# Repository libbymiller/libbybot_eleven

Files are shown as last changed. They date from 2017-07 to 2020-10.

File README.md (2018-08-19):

# libbybot_eleven

Eleventh incarnation of 
[libbybot](https://planb.nicecupoftea.org/2017/03/03/libbybot-presence-with-chromium-51-raspberry-pi-and-rtcmulticonnection-for-webrtc/), a cheapo, remotely-posable presence robot using [webRTC](https://en.wikipedia.org/wiki/WebRTC) and a Raspberry Pi, currently living in an IKEA lamp

Contains full instructions and code. 

Libbybot 8

The idea is that you run a headless browser on a Raspberry Pi in the lamp, and connect to it remotely via a laptop or phone using a browser (Chrome or Firefox).

You need to do the [server](/server) part of this first, then set up the [arduino](/arduino) and [pi](/pi). Construction instructions are in [doc](doc/)

## What you'll need:

 * Time: this takes a few hours at least even if you know what you are doing. It's not a quick project.
 * Raspberry Pi 3 (other versions don't have the oomph to run chromium and do video, though they can do audio, if you don't want to "see").
 * an official [Raspberry pi power cable](https://shop.pimoroni.com/products/raspberry-pi-universal-power-supply) - we're using a lot of amps! else you may get strange outages.
 * IKEA EXPRESSIVO lamp (discontinued, but most people have one at home, ask around). Or [this (thanks Barnoid!)](http://cpc.farnell.com/lloytron/l1101bk/lamp-desk/dp/LA04023) looks very similar.
 * [long (45cm) Raspberry Pi camera cable](https://shop.pimoroni.com/products/raspberry-pi-camera-cable)
 * [Raspberry Pi camera](https://shop.pimoroni.com/products/raspberry-pi-camera-module-v2-1-with-mount)
 * a [Sennheiser USB speaker / mic](http://www.exteradirect.co.uk/product/sennheiser/sp20-portable-speakerphone-usb-&-3.5mm/3258/)
 * 2 x 9g servos, small as you can get them ([e.g.](http://www.ebay.co.uk/itm/Mini-SG90-SG-90-Gear-9g-Micro-Servo-For-RC-Airplane-Helicopter-Car-Boat-Arduino/252297215595)). The blue type are the ones you need - the black ones are fractionally too long.
 * a [tiny breadboard](https://shop.pimoroni.com/products/colourful-mini-breadboard)
 * 6 x MM jumper cables 
 * 3 x MF jumper cables 
 * Arduino nano (e.g. a [clone](http://www.ebay.co.uk/itm/Mini-USB-Nano-V3-0-ATmega328P-CH340-5V-16MHz-SOLDERED-HEADS-Arduino-UK-/262738901345))
 * an old CD or a [custom laser cut shape](doc/laser_cut_base) - and 6 x 3mm diameter ball barings
 * little rubber feet ([e.g.](https://www.amazon.co.uk/Domed-Rubber-Buffers-Kitchen-Doors/dp/6040143746/ref=sr_1_1))
 * 1 thin small cable tie
 * two pieces of 2cm x 1cm x 3mm (or 1 x 5-6mm) plastic or something equally tough
 * two M2 plastic bolts

and

 * Something to cut holes in the lamp's plastic like a dremel (you can just about manage with a hacksaw and drill, but it's messy) plus suitable eye protection
 * a hacksaw
 * a phillip's head screwdriver
 * a gluegun
 * a vice
 * a pen
 * a tape measure

and, once you're up and running

 * a friendly helper in the remote place where you want to be, to plug the lamp in

The only really expensive thing is the speaker / mic. If you're going to use it seriously, this is the most important bit. I've tried a Jabra for this purpose but they are unreliable, I'm guessing they have heavier power 
requirements than the Sennheiser. The Sennheiser works really well - the best I've come across for this sort of thing.

Of course you don't have to use an IKEA ESPRESSIVO lamp. This project originally started off much more like a picture frame - you can see the pictures [here](https://planb.nicecupoftea.org/2017/03/03/libbybot-presence-with-chromium-51-raspberry-pi-and-rtcmulticonnection-for-webrtc/) - but it's hard to fit the speaker into some sort of sensible shape. My robot research has shown that showing my face to the participants of a teleconference is not necessary as long as I can hear, speak, see and move  a little (in that order).

More on how to actually fit it into the lamp is in [doc](doc/).

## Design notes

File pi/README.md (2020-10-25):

# Introduction

The idea is that you run a headless browser on the pi, and connect to it 
via a laptop or phone using a browser. 

You'll need a [server](/server) to connect to first.

More on how to actually fit it into the lamp, including assembling everything, is in 
[doc](doc/).

# Installation

This is mostly a matter of making sure the audio and video drivers are 
in place, and then running chromium on boot, together with a simple 
python server for controlling the servos.

## Set up the Pi with Buster (not Buster-lite)

[Here are full instructions for burning an SD card](https://www.raspberrypi.org/documentation/installation/installing-images/) or use [Etcher](https://etcher.io).

When it's done, still with the SD card in the card reader (you may have to unplug the reader / plug it in again), do

    touch /Volumes/boot/ssh 

(This is on a Mac; other OS you need to figure out where `boot` is mounted and create an empty file)

[Add in your wifi network creds](https://www.raspberrypi.org/blog/page/2/?fish#another-update-raspbian) to /Volumes/boot/wpa_supplicant.conf:

    nano /Volumes/boot/wpa_supplicant.conf

contents (the country first line is important, though it doesn't have to be GB, obviously):

    country=GB
    ctrl_interface=DIR=/var/run/wpa_supplicant GROUP=netdev
    update_config=1

    network={
       ssid="foo"
       psk="bar"
    }

or if you're going to move it around, you could [try this](https://planb.nicecupoftea.org/2015/12/04/raspberry-pi-create-an-access-point-for-easily-getting-limited-input-devices-on-wifi-chromecast-style/).

Eject the SD card and put it in a Pi3.

Log in, e.g. by using a screen and keyboard and mouse or by sharing your 
network over ethernet and sshing in, or sshing in over your network if 
you added the `wpa_supplicant.conf` credentials as above.

## Add audio and video drivers

    sudo nano /etc/modules

contents:

    i2c-dev
    snd-bcm2835
    bcm2835-v4l2

(bcm2835-v4l2 is the V4l2 video drivers for Chromium to pick up the camera; there used to be a [bug](https://stackoverflow.com/questions/25941171/how-to-get-gstreamer1-0-working-with-v4l2-raspicam-driver) but not any more)

## Enable USB audio

    sudo nano /boot/config.txt 

in contents

    #dtparam=audio=on ## comment this out

then

    sudo nano /lib/modprobe.d/aliases.conf

in contents

    #options snd-usb-audio index=-2 # comment this out

(I find USB audio on the linux / Pi very tricky and I'm not the only one. However, in 
recent Raspian versions USB audio seems to Just Work. The above is belt and braces. 
[More on linux 
audio](http://raspberrypi.stackexchange.com/questions/39928/unable-to-set-default-input-and-output-audio-device-on-raspberry-jessie).)

## Give the GPU more oomph

This is optional, but you'll get smoother video performance at the cost of the chip getting hotter...! ([more info](https://raspberrypi.stackexchange.com/a/1885)).

Edit config.txt

    sudo nano /boot/config.txt  

contents - add or edit:

    gpu_mem=192 

## Add autostart

    sudo nano /etc/xdg/lxsession/LXDE-pi/autostart

contents:

    @lxpanel --profile LXDE-pi
    @pcmanfm --desktop --profile LXDE-pi
    @xscreensaver -no-splash
    @xset s off
    @xset -dpms
    @xset s noblank
    #@v4l2-ctl --set-ctrl=rotate=270 # if you need to rotate the camera picture
    @/bin/bash /home/pi/start_chromium.sh

Add the files start_chromium and server.py from this directory into the pi 
homedirectory. Edit ```start_chromium.sh``` to refer to your server.

Make them executable:

    chmod a+x start_chromium.sh server.py

install the python server

    sudo pip install bottle

enable the camera and serial in ```interfacing options``` using

    sudo raspi-config

for serial, select 'no' for 'would you like a login shell to be accessible over 
serial?' and 'yes' to 'Would you like the serial port hardware to be enabled?'

Change the pi name and password

    sudo nano /etc/hostname
    sudo nano /etc/hosts
    passwd

## Assemble everything and test

Shutdown and unplug the pi, then - 

 * [connect the camera to the pi](https://www.raspberrypi.org/documentation/usage/camera/README.md)
 * connect the sennheiser to the pi
 * plug in the pi's power again

On your-server, check the logs of `server.js` and you'll see the number of the room 
it's connected to.

Connect to https://your-server:8443/remote.html#roomnumber on a laptop, 
in Chrome or Firefox. You should see whatever the Pi's camera is pointing at, 
and be able to hear too, and speak. 

Longer term, you need to figure out how to do notifications. There's a place in 
[server.js](/../server/server.js) where you can send a dm tweet or a slack notification 
for example.

More on how to actually fit it into the lamp, including adding the Arduino, is in 
[doc](doc/).

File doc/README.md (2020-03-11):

# Introduction

Allow a few hours for this.

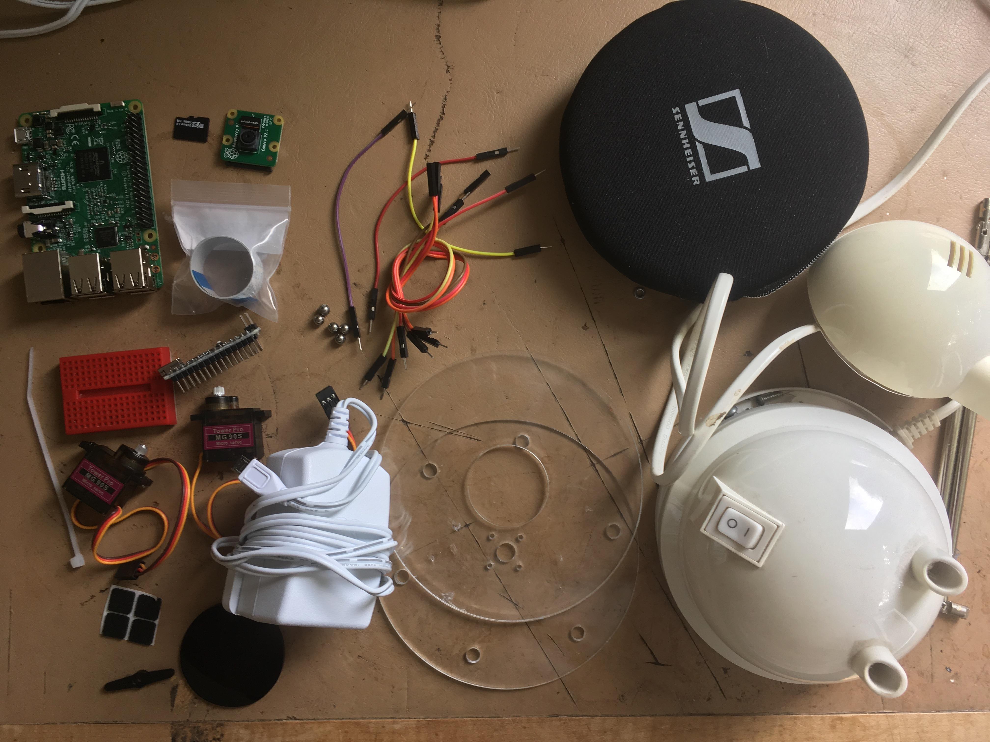
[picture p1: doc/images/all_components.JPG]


The idea is to hollow out the base to fit a Pi and and Arduino in it, and fit tiny servos to the top part (the 'head') and the base.

## Modify the case

Take your EXPRESSIVIO lamp, making sure it is unplugged from the mains, obviously, unscrew the base and remove and discard the transformer and related pieces, together with the power cable.

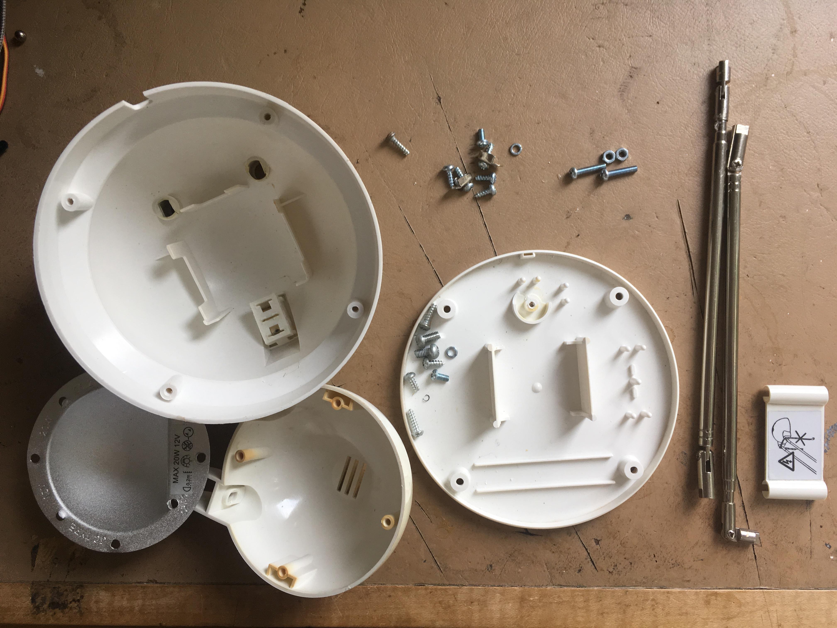
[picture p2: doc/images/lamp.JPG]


Remove the glass plate from the top, and the bulb and any bits of wires connected to it.

With pliers, snap off the inside segments of both parts of the base to make as much room as you can. 

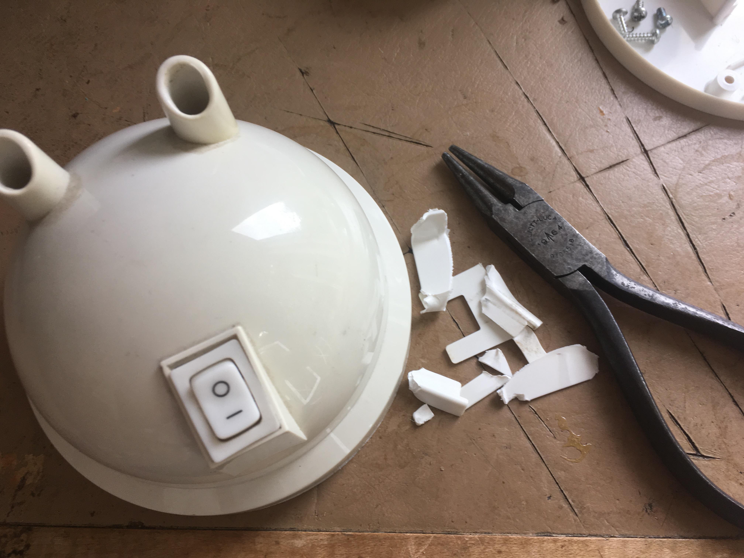
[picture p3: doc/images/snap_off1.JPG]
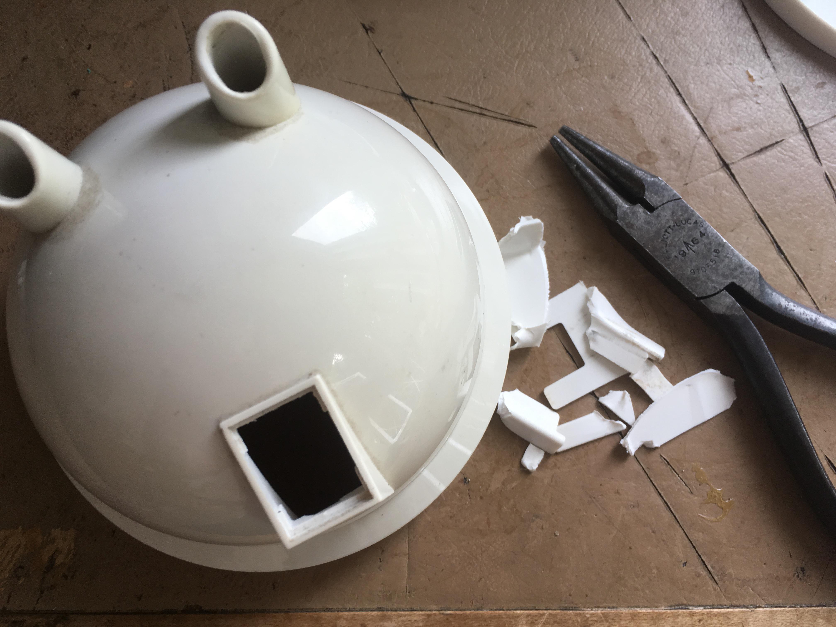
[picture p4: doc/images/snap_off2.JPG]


Carefully saw the backs off the top ariel covers. Don't saw off too much - just up to the curved point to make a straight line, and then saw the corner off the inside of each one.

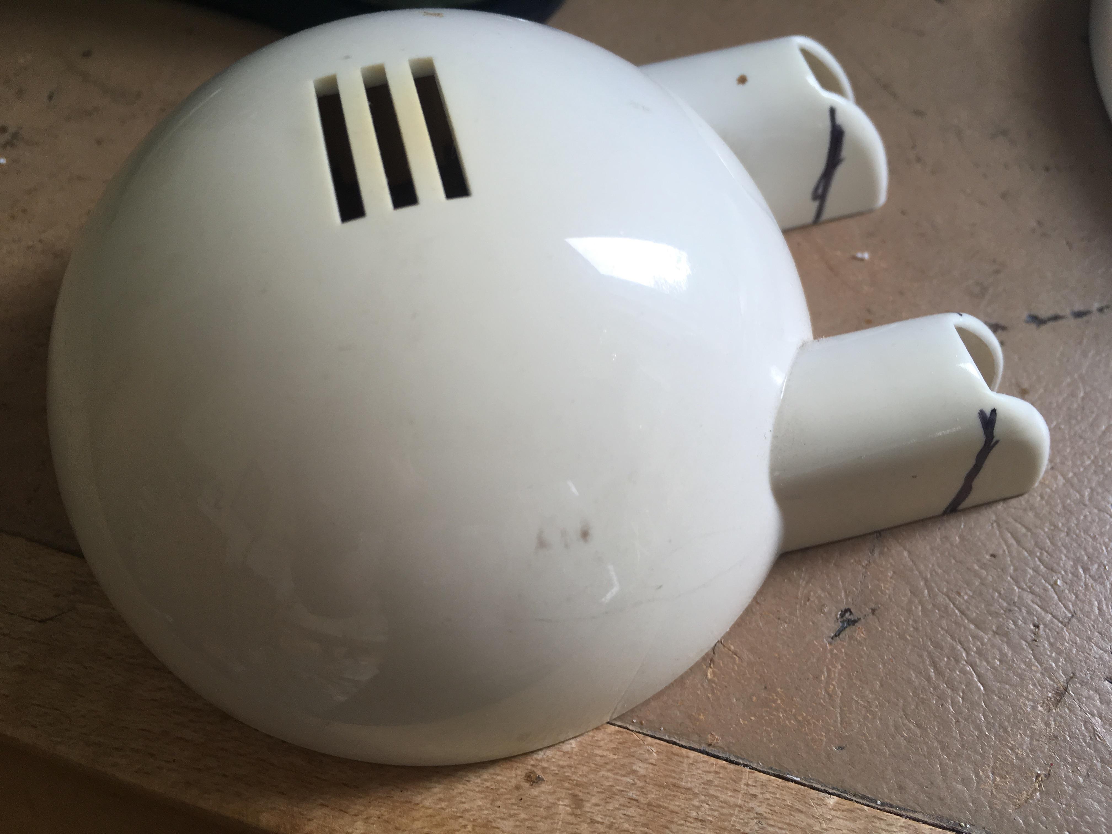
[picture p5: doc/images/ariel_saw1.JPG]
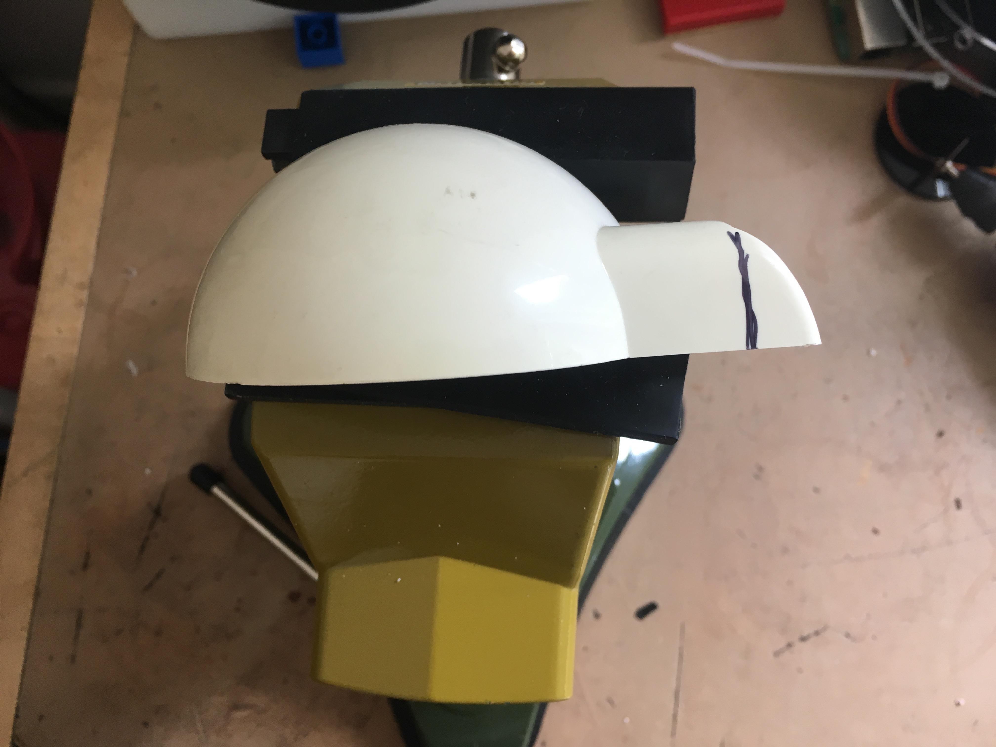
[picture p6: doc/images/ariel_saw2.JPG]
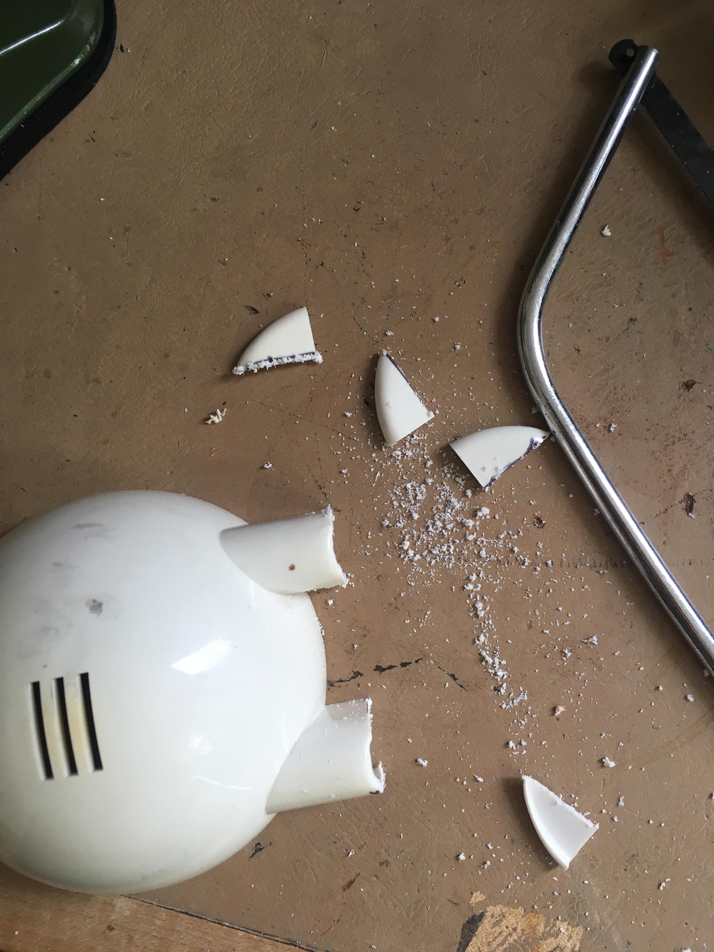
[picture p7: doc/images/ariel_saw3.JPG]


Saw or dremel a hole in the back of the base. This needs to be wide and deep enough to get a USB cable and a wifi camera cable into (it's also sometimes useful to be able to get the Ethernet cable in too if possible). About 1cm x 4cm half way between the bottoms of the ariels and the rim of the base will do the job. Tidy it up with sandpaper.

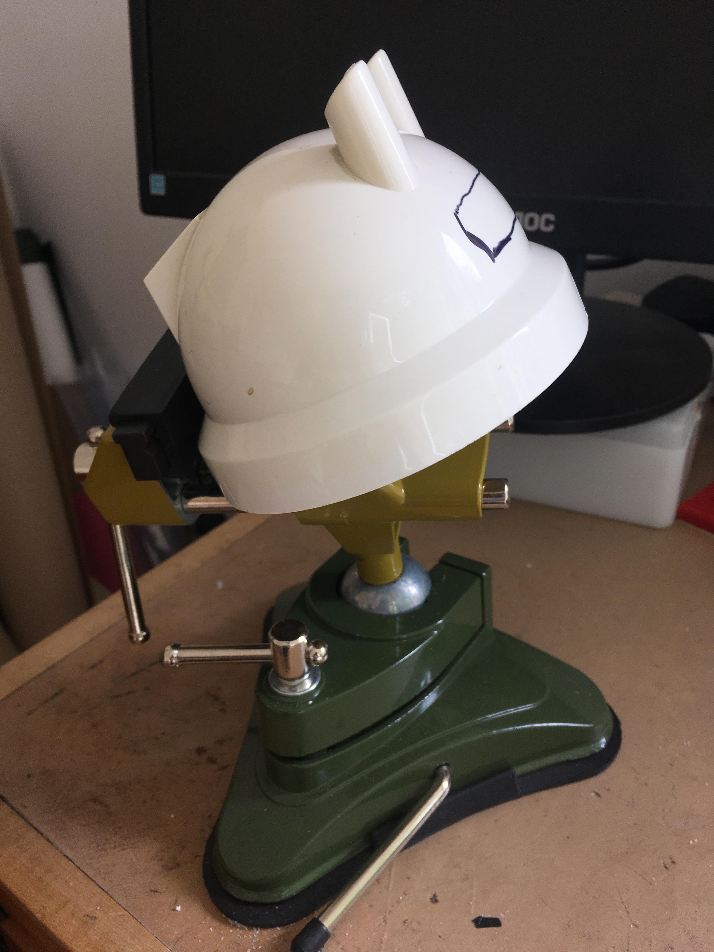
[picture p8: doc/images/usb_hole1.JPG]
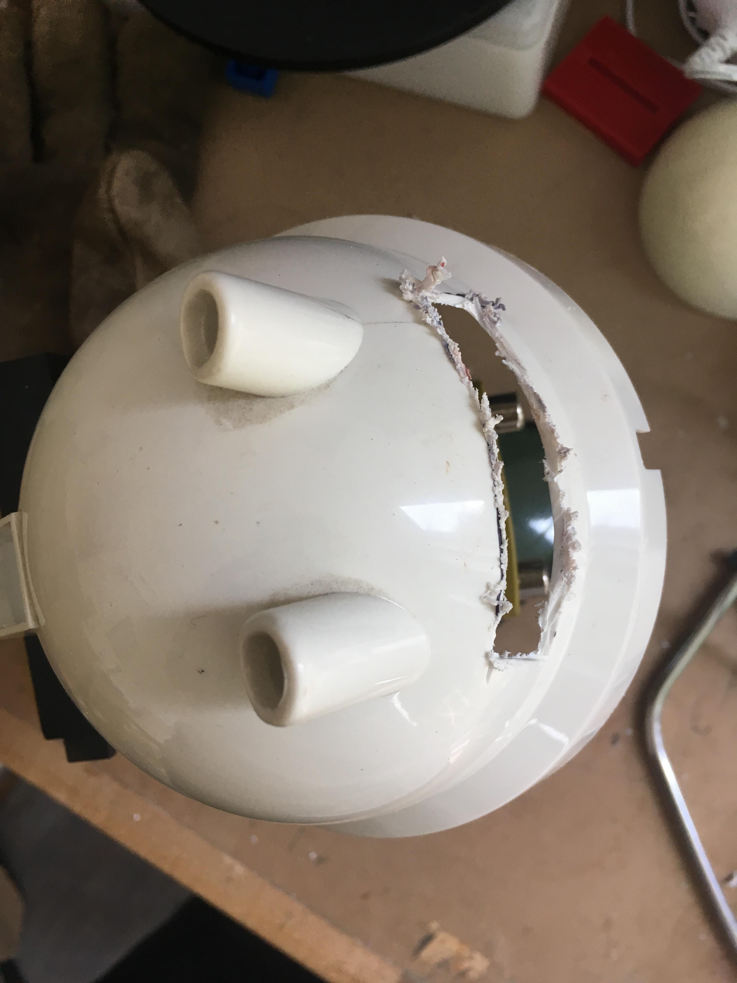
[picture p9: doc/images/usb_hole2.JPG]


Dremel or drill two holes in the centre of the flat base panel such that the servo exactly fits. 

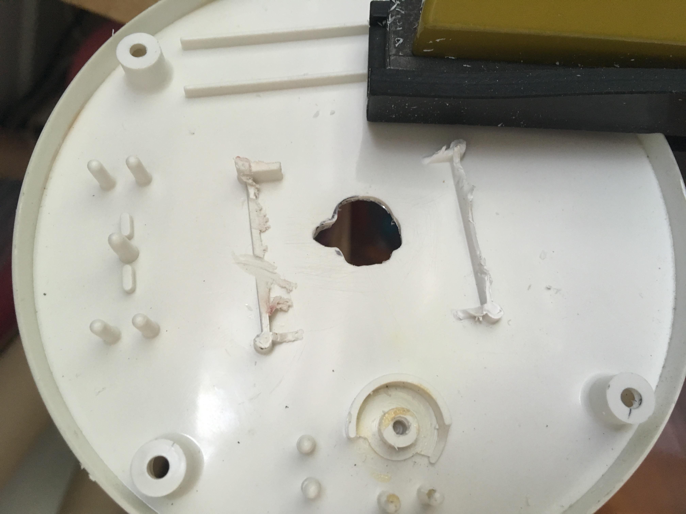
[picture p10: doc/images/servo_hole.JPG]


You'll also need to saw a small wedge out of the base to fit the power supply cable in. It's easier to do this at the end - see below.

## Connect the top servo

 * flash the arduino with the code in [arduino](/arduino)
 * push on the servo's one-sided horn (the plastic bit that you attach to the motor itself) - but don't screw it on yet
 * connect the servo to 5V (red), GND (brown or black) and D4 (orange)

Hold the servo with the horn facing you.

In the serial part of the arduino IDE, type "2 10". This is the lowest point for the 'head'. Re-position the horn if need be so it's parallel to the body of the servo.
 
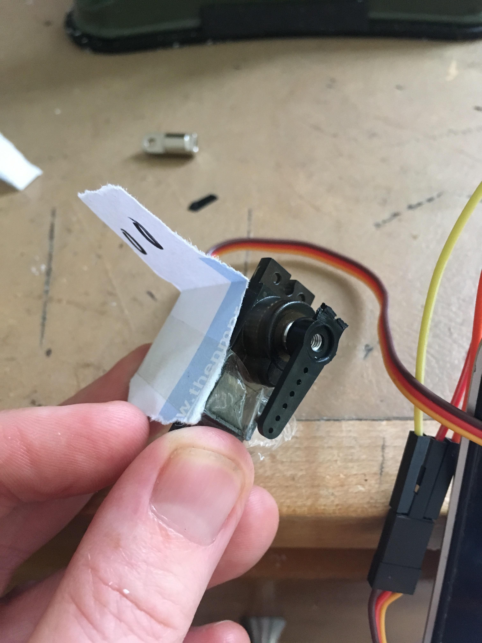
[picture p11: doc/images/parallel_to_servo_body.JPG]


Now type "2 60" in the Arduino IDE. This is the highest point of the head. Holding the horn with it facing you, the body of the servo should turn clockwise by 50 degrees. Type "2 10" again to get it back to its starting position. 

Now reassemble and position the lamp:
 * tighten the ariel's bottom screws as tight as they go
 * move the lamp so its head is as far bowed as it will go.

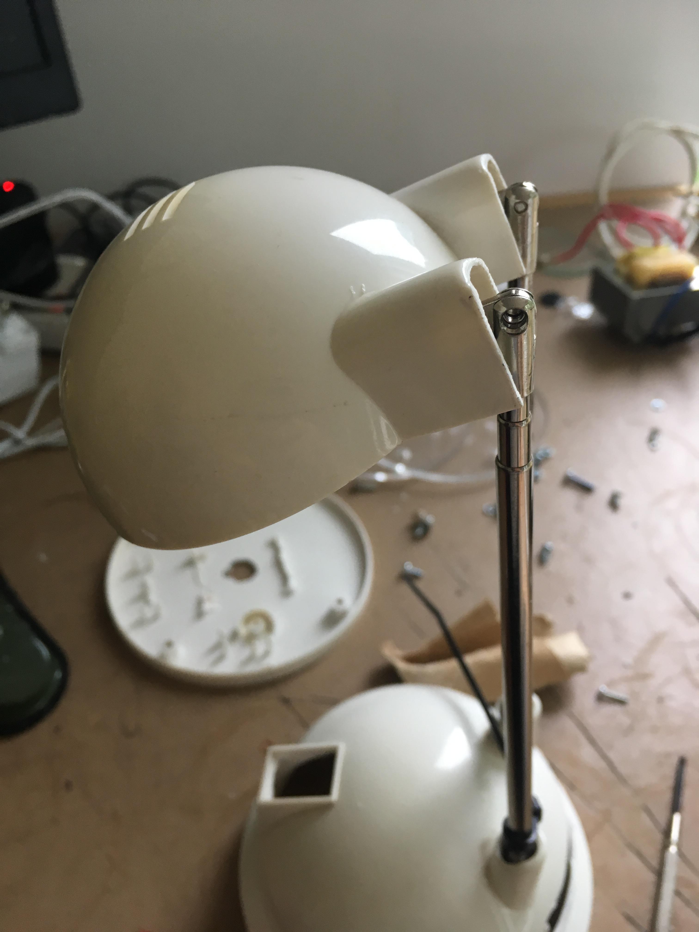
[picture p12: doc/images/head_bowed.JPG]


Replace the right hand screw at the top of the lamp with a servo and a screw through its spindle (you'll need to find a screw that's a bit longer than the usual one). Cable-tie the servo's horn to the downward ariel. Loosen the other screw so it is mobile.

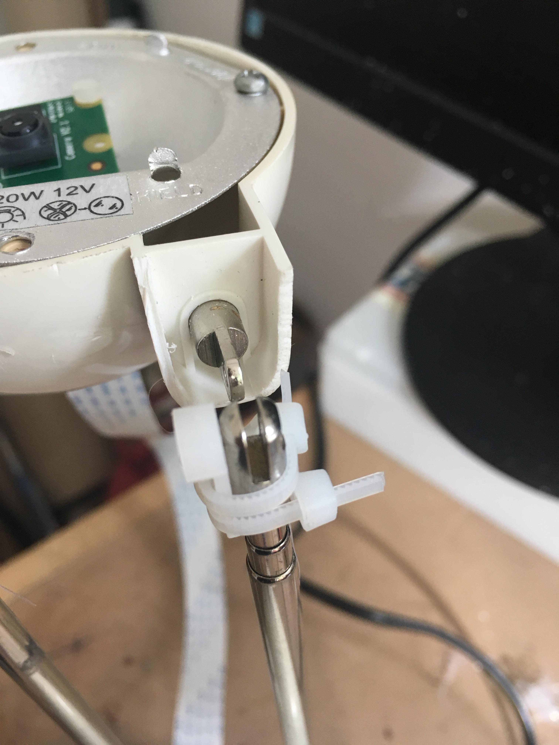
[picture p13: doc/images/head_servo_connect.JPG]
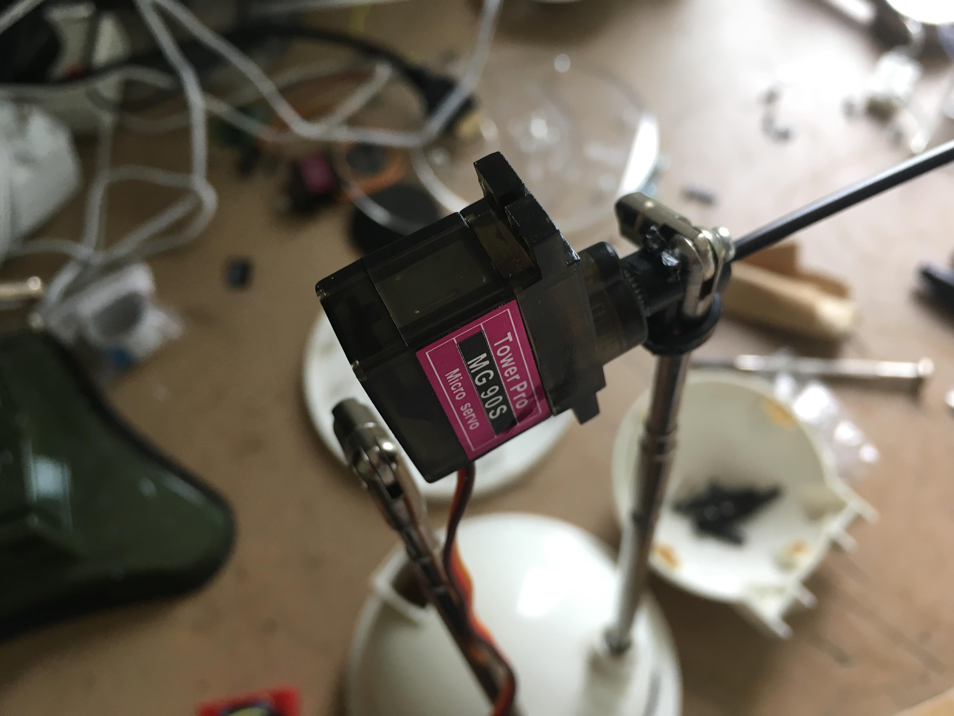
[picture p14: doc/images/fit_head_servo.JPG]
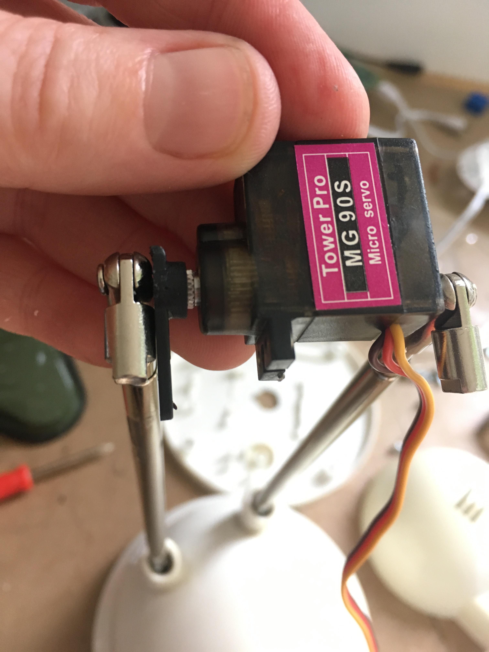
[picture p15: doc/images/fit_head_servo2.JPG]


Glue-gun one or two of the flat plastic pieces between the servo and the bottom of the lamp top (how many you need depends a bit on your servo's size and how much plastic you took off the lamp).

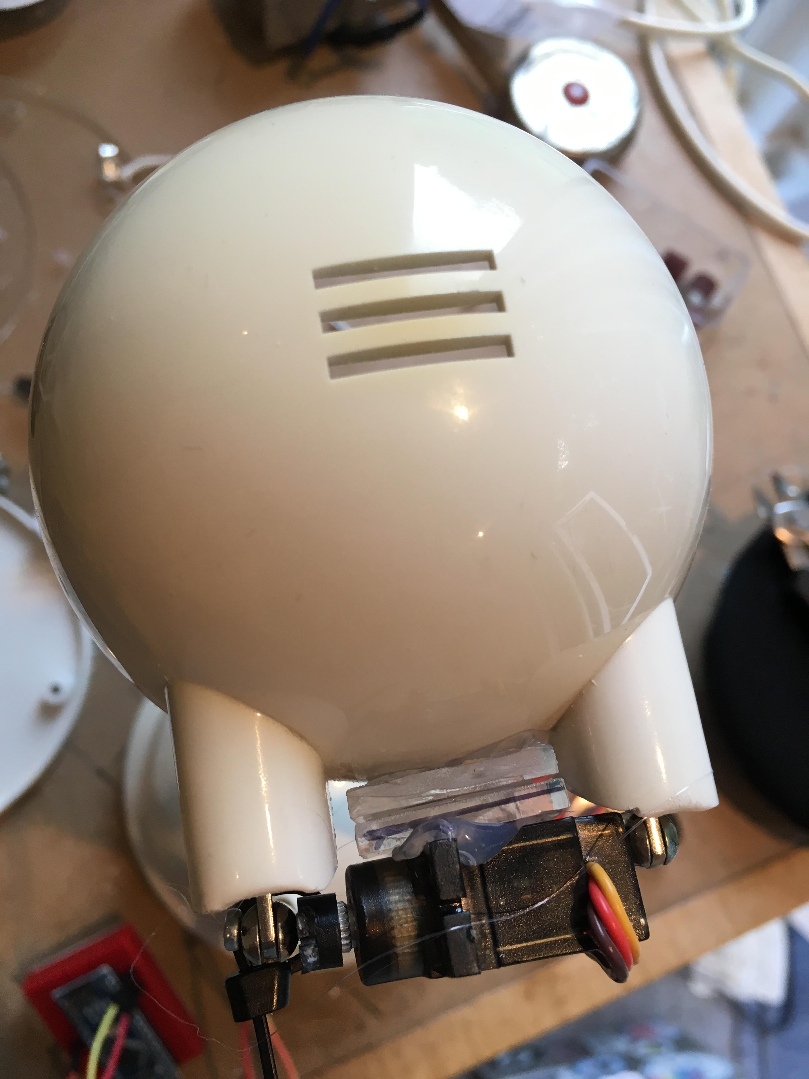
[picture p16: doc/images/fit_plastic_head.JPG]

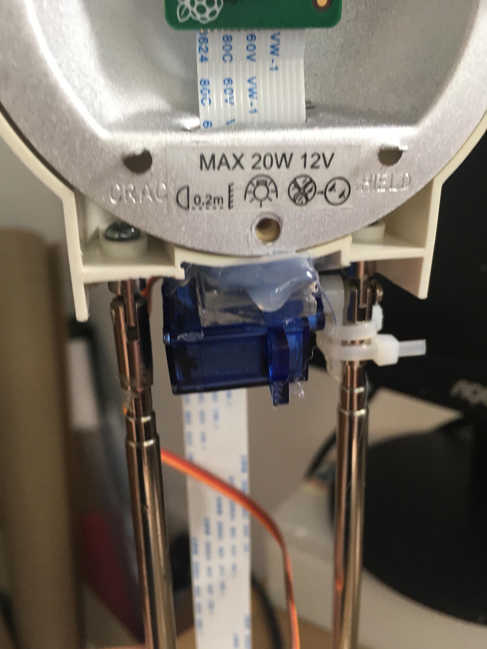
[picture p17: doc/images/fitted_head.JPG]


Test the servo again.

## Connect the bottom servo

 * connect the servo to 5V, GND and D3 (orange)
 * Figure out where 90 degrees is (using ("1 90") in serial)

Place that point at the front of the lamp.

Wedge the servo into the holes you made, glue-gunning it in as well.

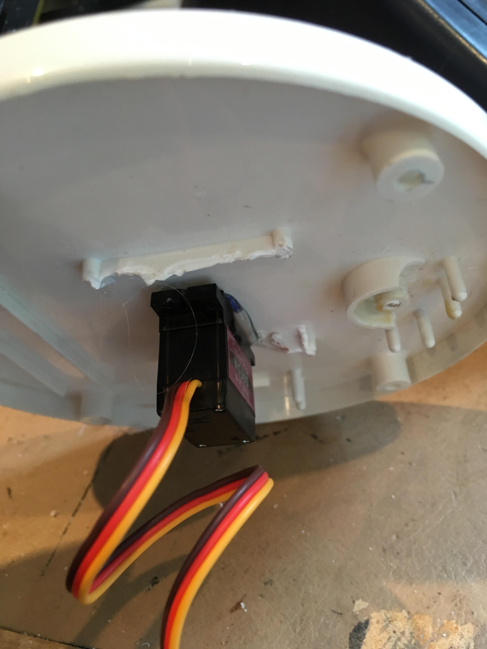
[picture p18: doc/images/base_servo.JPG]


When the glue has dried, test the servo again (e.g '1 10' '1 90' '1 170').

## Connect the arduino and the Pi

We're using a serial connection to save space.

On the Arduino you should have the top servo connected to pin D4 and the other to pin D3.

Connect:
 * 5v on Pi to 5v on the arduino (e.g. [GPIO physical numbering](https://www.raspberrypi.org/documentation/usage/gpio/) 2 or 4)
 * ground on the Pi to ground on the Arduino (e.g. GPIO physical numbering 6, 9 etc)
 * Pi's TDX (GPIO physical numbering pin 8) to Arduino's RX

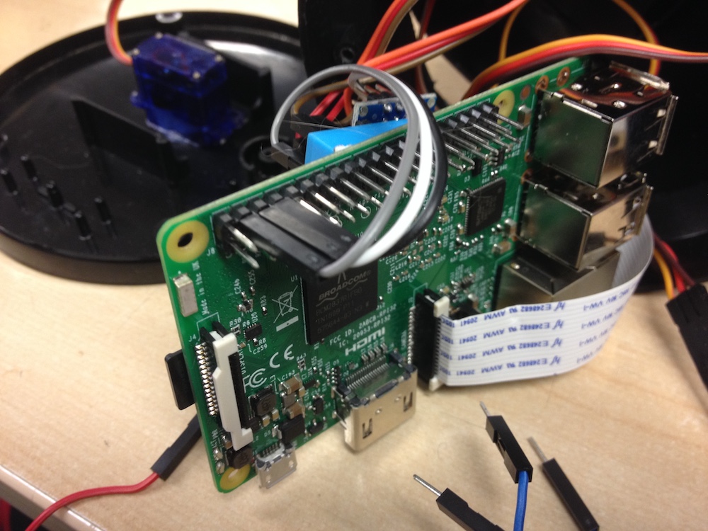
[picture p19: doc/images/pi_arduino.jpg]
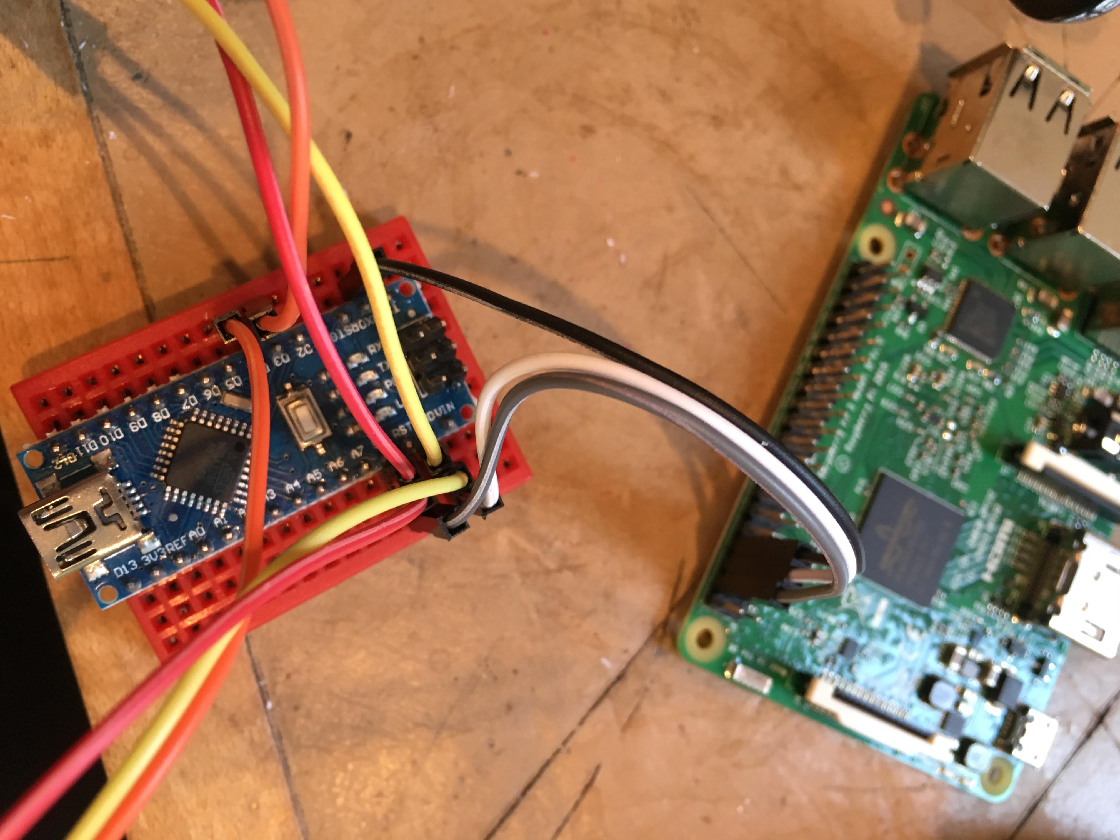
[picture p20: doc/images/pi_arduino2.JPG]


Normally you'd [need a voltage divider](https://oscarliang.com/raspberry-pi-and-arduino-connected-serial-gpio/) 
to do this serial communication, but because we're only going one way - from the 
Pi to the Arduino - we get away with it.

Stick or rest the breadboard to the back of the Pi.

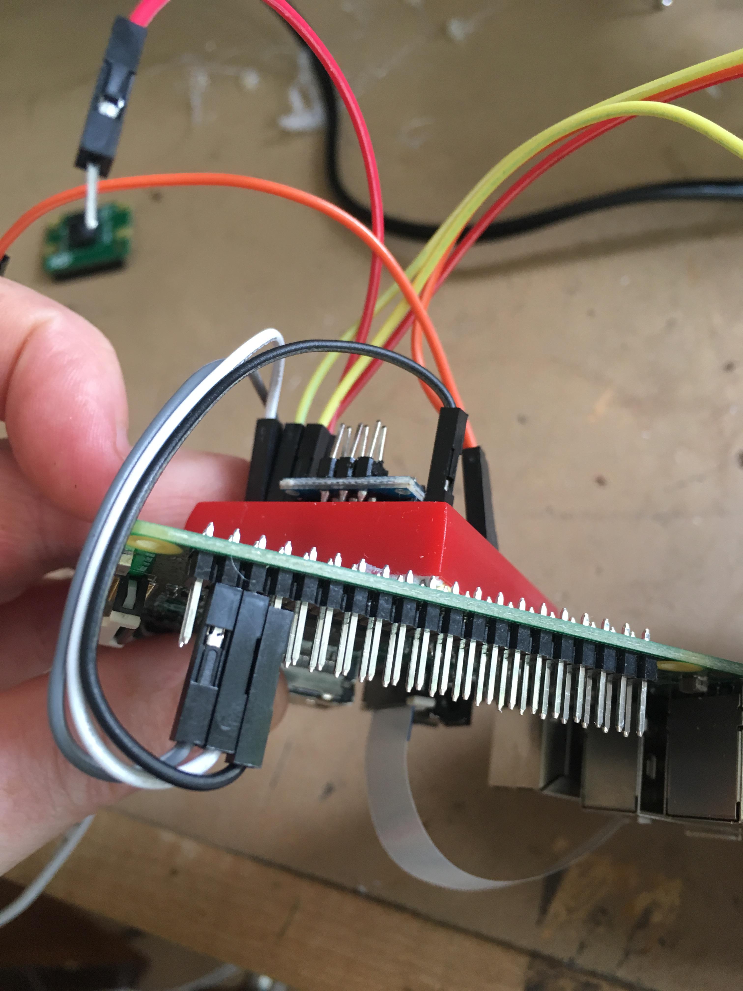
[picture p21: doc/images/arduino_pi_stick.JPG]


## Add the camera

Carefully widen the slit in the aluminum case at the bottom and thread the extra long camera cable through it. Connect and position the camera, screwing it (using plastic screws if you do) or glueing it into place.

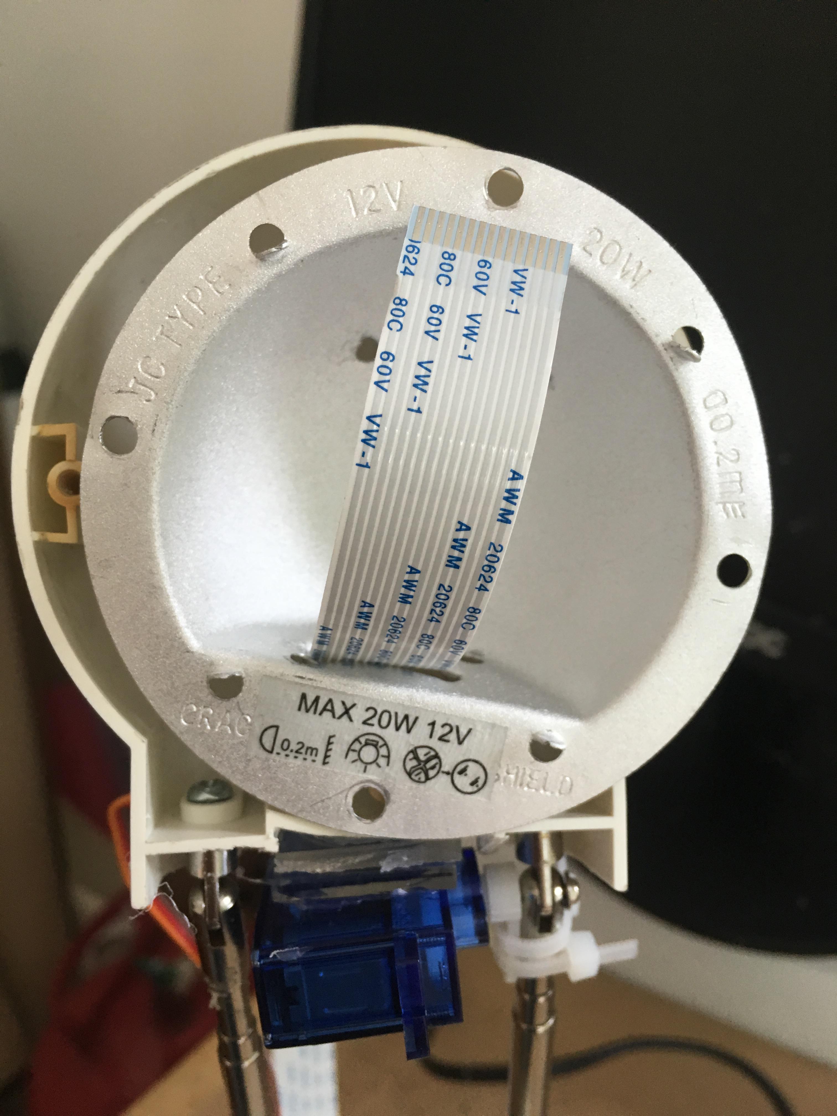
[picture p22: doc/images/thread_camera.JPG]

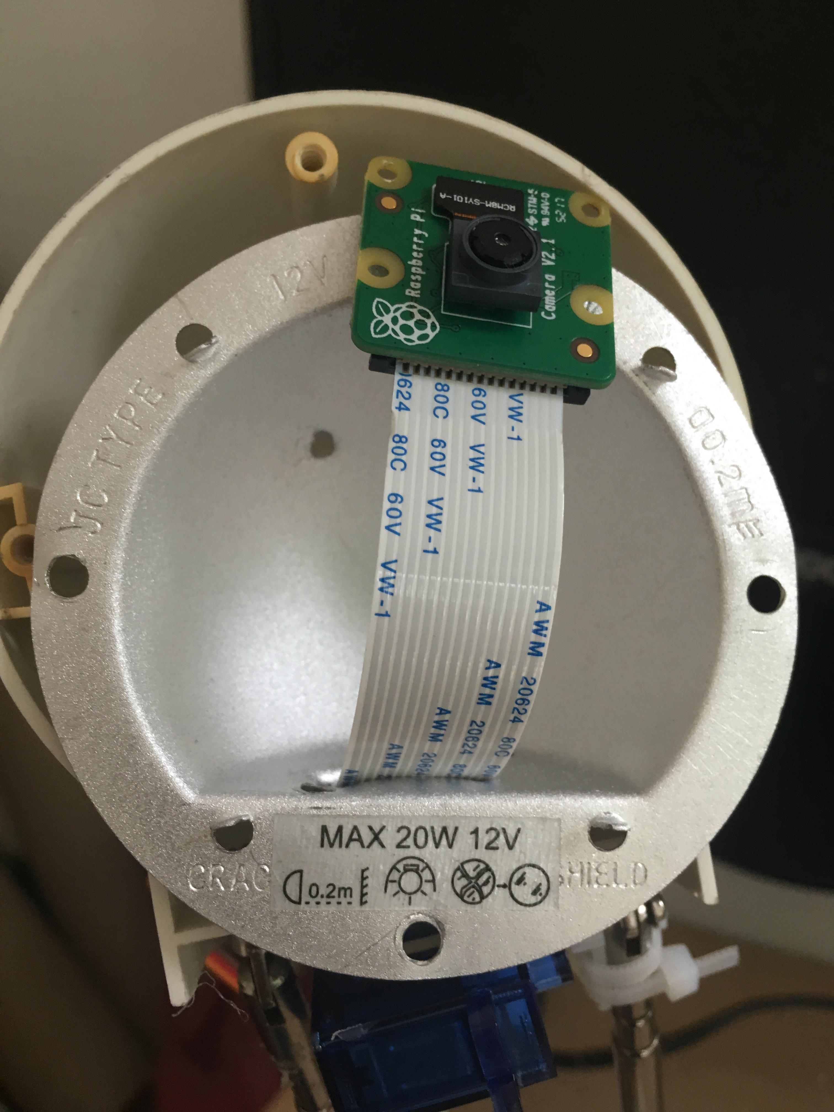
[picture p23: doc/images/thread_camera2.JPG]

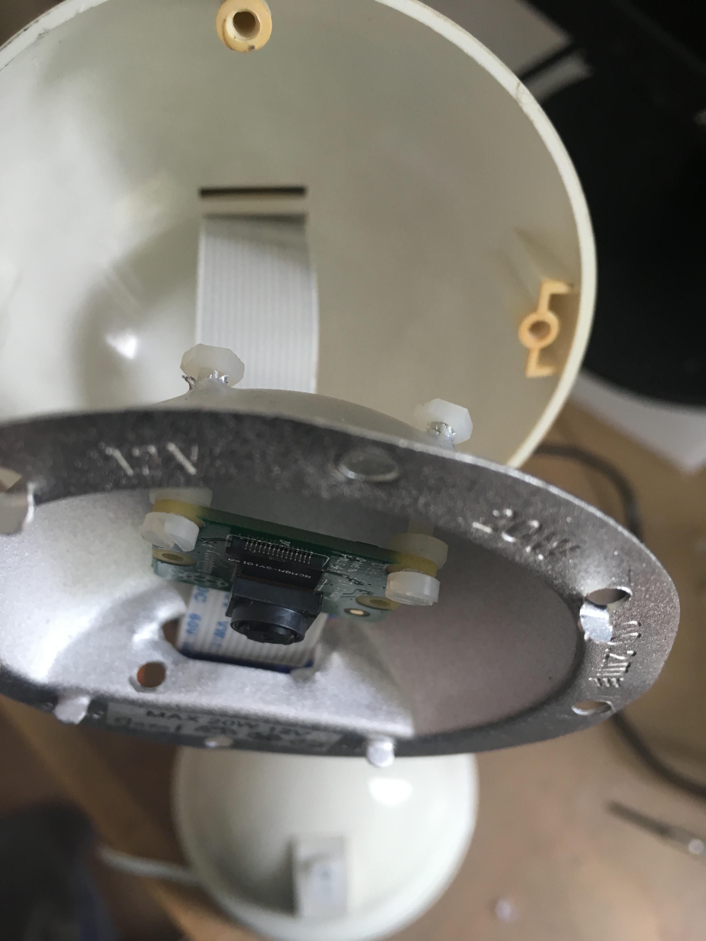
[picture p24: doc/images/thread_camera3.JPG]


Feed the other end into the slot you made in the base and attach it to the Pi (making sure the Pi is unplugged and that you're connecting it the [right way round](https://thepihut.com/blogs/raspberry-pi-tutorials/16021420-how-to-install-use-the-raspberry-pi-camera).) 

<a href="images/camera_base.JPG">

## Connect everything together

This is quite a wedge and it's why you need the smallest 9g servo you can find.

Basically the Pi goes in the bottom at an angle with the breadboard underneath the Pi. It needs to be placed at a downward angle so that the USB port is accessble through the slot, and so that there's room for the servo and the servo isn't squishing the camera cable.



First, make sure you've programmed the Arduino and got the Pi on the network you want to use it on, and that you've connected the Arduino via serial to the Pi (see above). You can't reprogramme the Arduino once it's in because it can't be programmed with the serial attached.

Connect the power cable to the Pi, and, making sure you have the lamp base the right way round (there's a notch at the back) carefully mark and saw a wedge out of the base for it to fit. It must not be forced or bend! You may also need to saw off the top of one of the base plate's screw casings (make sure you get the right one).

<a href="images/power_hole2.JPG">

Connect the Sennheiser through the slot to the USB port.

This is a good time to test everything works - plug it in and check the server for messages about the url to use and load the url in Chrome. 

If all is well, replace the bottom plate - you may need to twist it slightly to get it on its rails. Screw it on, omitting the screw near where you cut the notch. 

If you have laser-cut the base components in the [laser_cut_base](laser_cut_base/) directory, glue the servo horn to base 1 with the notch facing through the hole, glue base 2 to base 1, put the ball bearings in the holes and attach the 
two parts of the servo together, screwing them in. Otherwise, glue the servo horn part to the CD base and add rubber feet.



If all is well, you're ready to go. Plug it in!

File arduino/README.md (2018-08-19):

# Introduction

This is a very simple piece of code that expects commands over serial of the form:

    number degrees [p|n]

e.g. 

```1 90``` means turn servo 1 to absolute position of 90 degrees.

```1 10 p``` means turn servo 1 10 degrees in a positive direction.

```2 10 n``` means turn servo 2 10 degrees in a negative direction.

Servo 1 is the base (rotating) and goes in arduino pin 3. Servo 2 is the "head" of the lamp (nodding, etc) and goes in arduino pin 4. Servos 3 and 4 are not used (I'm using them in later versions to give the shoulders more sass).

[server.py](../pi/server.py) uses groups of these commands passed through from the web browser via webRTC sockets and passes them via serial to the arduino.

# Installation

If you are using a Nano clone, you'll need 
[drivers](https://kig.re/2014/12/31/how-to-use-arduino-nano-mini-pro-with-CH340G-on-mac-osx-yosemite.html).

Note that you'll need to disconnect the serial connection from the Raspberry pi to flash the arduino (this catches me out every time). And then plug it back in again (this also catches me out every time).

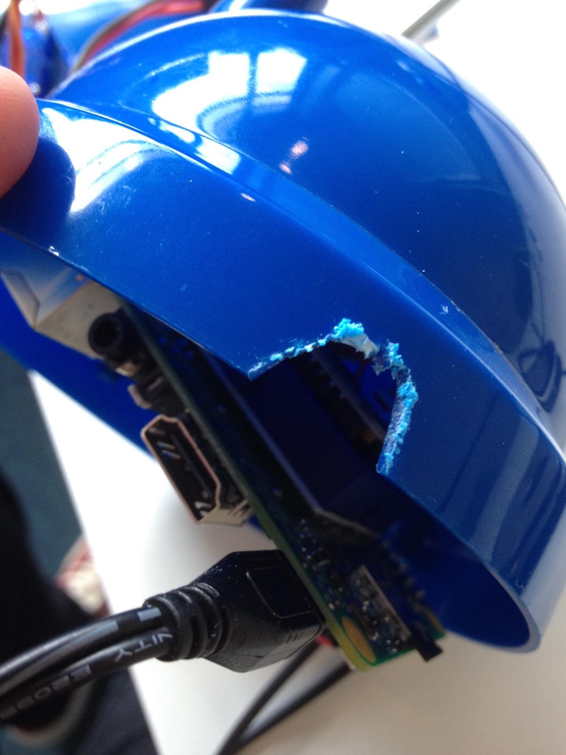
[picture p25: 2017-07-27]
doc/images/saw_a_notch.jpg

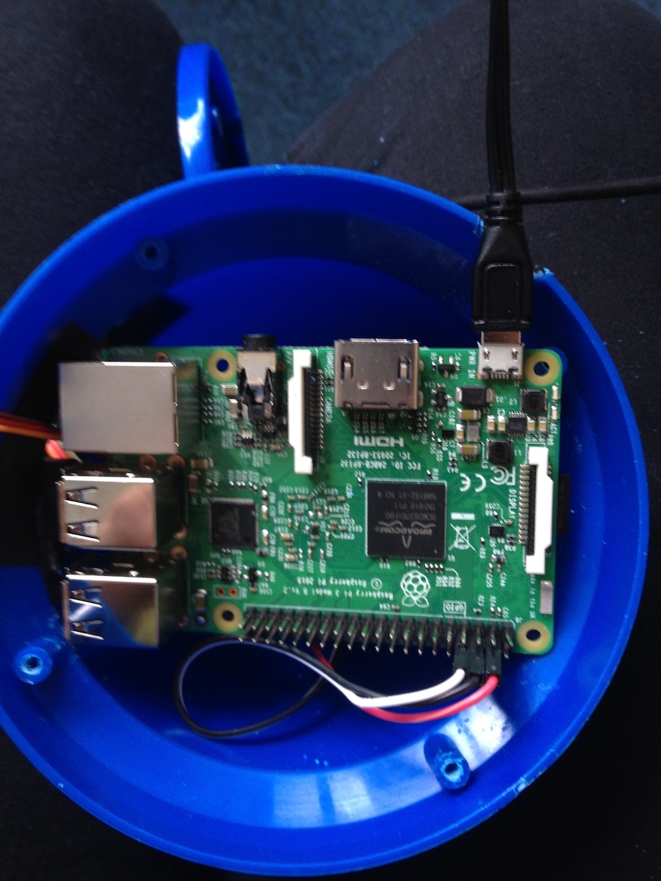
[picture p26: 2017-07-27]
doc/images/fit_the_psu.jpg

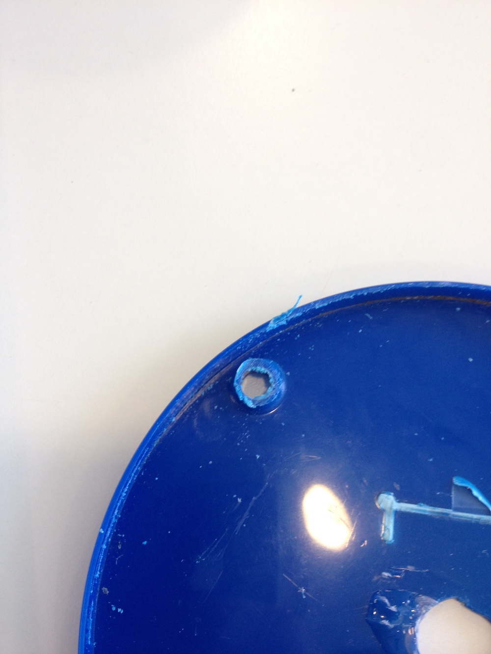
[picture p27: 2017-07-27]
doc/images/saw_the_screw_casing.jpg

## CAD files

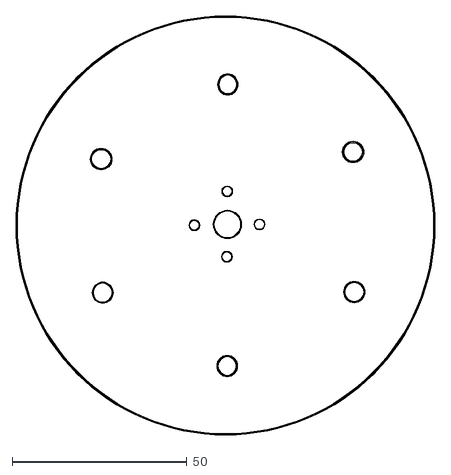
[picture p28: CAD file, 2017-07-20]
doc/laser_cut_base/base1.dxf
120.0 x 120.0

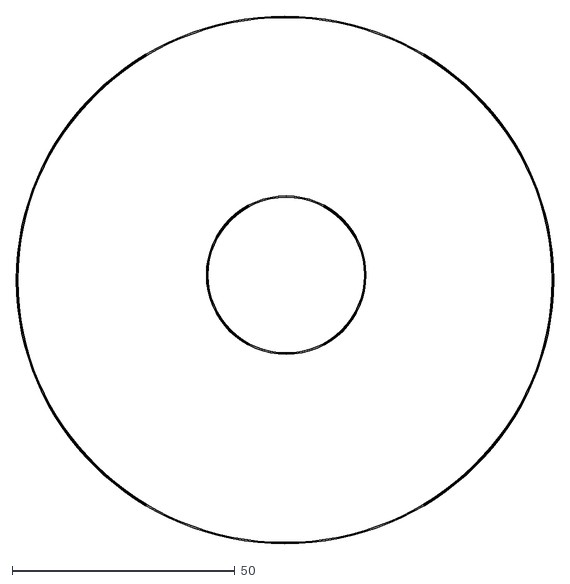
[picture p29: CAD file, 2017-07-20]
doc/laser_cut_base/base2.dxf
120.6 x 118.4

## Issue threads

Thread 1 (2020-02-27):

Determining if setup of server was done correctly

cvaldez83, 2020-02-27:
Hi, a noobie here...  I've followed the installation instructions for the [server setup](https://github.com/libbymiller/libbybot_eleven/tree/master/server).  I did the last step of typing "nohup nodejs server.js > /dev/null 2>&1 &" but not sure what is suppose to happen. Before moving on to setting up the pi, how do I know if the server is working?

libbymiller, 2020-02-28:
ahoy, good question - it's actually quite easy to check. Open this in one browser window (Chrome, ideally, on a laptop or phone):

https://yourserver:8443/libbybot/bot11.html#1234

(it should ask for your camera / mic). This is the one that the Pi will use when you have made it.
Open this in another window, can br the same browser or a different one, same device is ok if it's a laptop:

https://yourserver:8443/libbybot/remote11.html#1234

- this is the one that you will load to use the robot. The bar across the top of remote11 should go green and say 'connected'.

The "#1234" can be anything but must be the same.

If it doesn't work, check your certificates and so on - there should be some info in the `nohup.out` file or in one of the browser consoles.

Hope that helps.

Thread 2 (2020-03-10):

Why do we need an Arduino?

djmaze, 2020-03-10:
It should be possible to control the servos via the Pi GPIOs directly, shouldn't it?

libbymiller, 2020-03-10:
Thanks! Yes you could, doing something like [this](https://github.com/libbymiller/zamia_listening_pi/blob/master/kaldi_and_move.py#L45). When I did some initial experiments (a while ago now) there were delays in the responsiveness of the Pi, because a Pi3 is running at high capacity when running Chromium headlessly. But I didn't experiment much and it could definitely be done.

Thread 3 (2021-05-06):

SSL_CTX_use_certificate:ee key too small

man4567890, 2021-05-06:
Hi
I'm running Ubuntu 21.04 and I get this error when starting the server
```
nodejs server.js
_tls_common.js:129
      c.context.setCert(cert);
                ^

Error: error:140AB18F:SSL routines:SSL_CTX_use_certificate:ee key too small
    at Object.createSecureContext (_tls_common.js:129:17)
    at Server.setSecureContext (_tls_wrap.js:1328:27)
    at Server (_tls_wrap.js:1186:8)
    at new Server (https.js:70:14)
    at Object.createServer (https.js:94:10)
    at Object.<anonymous> (/var/www/iot-digitata.com/RTCMultiConnection/server.js:270:26)
    at Module._compile (internal/modules/cjs/loader.js:999:30)
    at Object.Module._extensions..js (internal/modules/cjs/loader.js:1027:10)
    at Module.load (internal/modules/cjs/loader.js:863:32)
    at Function.Module._load (internal/modules/cjs/loader.js:708:14) {
  library: 'SSL routines',
  function: 'SSL_CTX_use_certificate',
  reason: 'ee key too small',
  code: 'ERR_SSL_EE_KEY_TOO_SMALL'
}

My letsencrypt seems to be ok
```
sudo certbot --apache -d xxxxxxx

Saving debug log to /var/log/letsencrypt/letsencrypt.log
Plugins selected: Authenticator apache, Installer apache
Cert not yet due for renewal

You have an existing certificate that has exactly the same domains or certificate name you requested and isn't close to expiry.
(ref: /etc/letsencrypt/renewal/xxxxxx)

What would you like to do?
- - - - - - - - - - - - - - - - - - - - - - - - - - - - - - - - - - - - - - - -
1: Attempt to reinstall this existing certificate
2: Renew & replace the certificate (may be subject to CA rate limits)
- - - - - - - - - - - - - - - - - - - - - - - - - - - - - - - - - - - - - - - -
Select the appropriate number [1-2] then [enter] (press 'c' to cancel): 1
Keeping the existing certificate
Deploying Certificate to VirtualHost /etc/apache2/sites-enabled/xxxxxxx-le-ssl.conf
Enhancement redirect was already set.

- - - - - - - - - - - - - - - - - - - - - - - - - - - - - - - - - - - - - - - -
Congratulations! You have successfully enabled https://xxxx
- - - - - - - - - - - - - - - - - - - - - - - - - - - - - - - - - - - - - - - -

IMPORTANT NOTES:
 - If you like Certbot, please consider supporting our work by:

   Donating to ISRG / Let's Encrypt:   https://letsencrypt.org/donate
   Donating to EFF:                    https://eff.org/donate-le
```

:/var/www/iot-digitata.com/RTCMultiConnection$

Also when you say
Add a new directory 'libbybot', and add the html and javascript files from this github repo directory into that directory.
Where must the libbybot directory be, under /var/www/xxxxxxxxxxx/RTCMultiConnection$ ?

```
Thanks

libbymiller, 2022-04-04:
It's a bit late for you, but I just ran into this myself. Issue is that the default is some fake keys in the RTCMulticonnection repo, which are not overridden by the fields in server.js. You need to update config.json with the keys, something like this:

```
cat config.json
{
  "socketURL": "/",
  "dirPath": "",
  "homePage": "/",
  "socketMessageEvent": "RTCMultiConnection-Message",
  "socketCustomEvent": "RTCMultiConnection-Custom-Message",
  "port": "9001",
  "enableLogs": "false",
  "autoRebootServerOnFailure": "false",
  "isUseHTTPs": "true",
  "sslKey": "/etc/letsencrypt/live/libbybot.example.com/privkey.pem",
  "sslCert": "/etc/letsencrypt/live/libbybot.example.com/fullchain.pem",
  "sslCabundle": "/etc/letsencrypt/live/libbybot.example.com/chain.pem",
  "enableAdmin": "false",
  "adminUserName": "username",
  "adminPassword": "password"
}
```

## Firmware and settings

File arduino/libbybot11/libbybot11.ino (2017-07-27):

#include <Servo.h>

#define SERVOPIN1 3
#define SERVOPIN2 4
#define SERVOPIN3 5
#define SERVOPIN4 6

Servo myservo;  // create servo object to control a servo

// variable to store the servo position
int last_pos1 = 0;
int last_pos2 = 0;

//not currently used
int last_pos3 = 0;
int last_pos4 = 0;

void setup() {

  pinMode(LED_BUILTIN, OUTPUT);
  Serial.begin(9600);

}

int which_motor;
int motor_position;
String sign;
String str;

void loop() 
{
    if(Serial.available() > 0)
    {
        str = Serial.readStringUntil('\n');
        Serial.println("str is ");
        Serial.println(str);
        String xval = getValue(str, ' ', 0);
        String yval = getValue(str, ' ', 1);

        //for relative values
        String rval = getValue(str, ' ', 2);
        
        which_motor = xval.toInt();
        motor_position = yval.toInt();
        sign = rval;
        sign.trim();
        
        Serial.println("sign is");
        Serial.println(sign);
        Serial.println("which_motor is ");
        Serial.println(which_motor);
        Serial.println("motor_position is ");
        Serial.println(motor_position);
        
        switch(which_motor){
        case 1:
          myservo.attach(SERVOPIN1);  
          if(sign == "p"){
             motor_position = last_pos1 + motor_position;
             Serial.println("p moving to ");
             Serial.println(motor_position);
          }else if(sign == "n"){
             motor_position = last_pos1 - motor_position;   
             Serial.println("n moving to ");
             Serial.println(motor_position);
          }
          if(last_pos1 < motor_position){
           for (int pos = last_pos1; pos <= motor_position; pos += 1) { // goes from 0 degrees to 180 degrees
             // in steps of 1 degree
             myservo.write(pos);// tell servo to go to position in variable 'pos'
             delay(15);          // waits 15ms for the servo to reach the position
             last_pos1 = pos;
           }
          }else{
           for (int pos = last_pos1; pos >= motor_position; pos -= 1) { // goes from 0 degrees to 180 degrees
             // in steps of 1 degree
             myservo.write(pos);// tell servo to go to position in variable 'pos'
             delay(15);                       // waits 15ms for the servo to reach the position
             last_pos1 = pos;
           }              
          }
          myservo.detach();
          break;
        case 2:
          myservo.attach(SERVOPIN2);
          if(sign == "p"){
             motor_position = last_pos2 + motor_position;
          }else if(sign == "n"){
             motor_position = last_pos2 - motor_position;   
          }
          if(last_pos2 < motor_position){
           for (int pos = last_pos2; pos <= motor_position; pos += 1) { // goes from 0 degrees to 180 degrees
             // in steps of 1 degree
             myservo.write(pos);// tell servo to go to position in variable 'pos'
             delay(15);                       // waits 15ms for the servo to reach the position
             last_pos2 = pos;
           }
          }else{
           for (int pos = last_pos2; pos >= motor_position; pos -= 1) { // goes from 0 degrees to 180 degrees
             // in steps of 1 degree
             myservo.write(pos);// tell servo to go to position in variable 'pos'
             delay(15);                       // waits 15ms for the servo to reach the position
             last_pos2 = pos;
           }              
          }
          myservo.detach();
          break;
        case 3:
          myservo.attach(SERVOPIN3);          
          if(sign == "p"){
             motor_position = last_pos3 + motor_position;
          }else if(sign == "n"){
             motor_position = last_pos3 - motor_position;   
          }
          if(last_pos3 < motor_position){
           for (int pos = last_pos3; pos <= motor_position; pos += 1) { // goes from 0 degrees to 180 degrees
             // in steps of 1 degree
             myservo.write(pos);// tell servo to go to position in variable 'pos'
             delay(15);                       // waits 15ms for the servo to reach the position
             last_pos3 = pos;
           }
          }else{
           for (int pos = last_pos3; pos >= motor_position; pos -= 1) { // goes from 0 degrees to 180 degrees
             // in steps of 1 degree
             myservo.write(pos);// tell servo to go to position in variable 'pos'
             delay(15);                       // waits 15ms for the servo to reach the position
             last_pos3 = pos;
           }              
          }
          break;
          myservo.detach();
        case 4:
          myservo.attach(SERVOPIN4);          
          if(sign == "p"){
             motor_position = last_pos4 + motor_position;
          }else if(sign == "n"){
             motor_position = last_pos4 - motor_position;  
          }
          if(last_pos4 < motor_position){
           for (int pos = last_pos4; pos <= motor_position; pos += 1) { // goes from 0 degrees to 180 degrees
             // in steps of 1 degree
             myservo.write(pos);// tell servo to go to position in variable 'pos'
             delay(15);                       // waits 15ms for the servo to reach the position
             last_pos4 = pos;
           }
          }else{
           for (int pos = last_pos4; pos >= motor_position; pos -= 1) { // goes from 0 degrees to 180 degrees
             // in steps of 1 degree
             myservo.write(pos);// tell servo to go to position in variable 'pos'
             delay(15);                       // waits 15ms for the servo to reach the position
             last_pos4 = pos;
           }              
          }
          myservo.detach();
          break;
        }        
        //blink(x);
    }
}

// only used for testing
int blink(int i){
        if(i){
          for(int j=0; j< i; j++){
           digitalWrite(LED_BUILTIN, HIGH);   // turn the LED on (HIGH is the voltage level)
           delay(1000);                       // wait for a second
           digitalWrite(LED_BUILTIN, LOW);    // turn the LED off by making the voltage LOW
           delay(1000);
          } 
        }
}

// https://arduino.stackexchange.com/questions/1013/how-do-i-split-an-incoming-string
String getValue(String data, char separator, int index)
{
    int found = 0;
    int strIndex[] = { 0, -1 };
    int maxIndex = data.length() - 1;

    for (int i = 0; i <= maxIndex && found <= index; i++) {
        if (data.charAt(i) == separator || i == maxIndex) {
            found++;
            strIndex[0] = strIndex[1] + 1;
            strIndex[1] = (i == maxIndex) ? i+1 : i;
        }
    }
    return found > index ? data.substring(strIndex[0], strIndex[1]) : "";
}

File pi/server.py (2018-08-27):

#!/usr/bin/python
from bottle import run, route, request, response
import subprocess
import serial
import sys
import time
import os

# http://stackoverflow.com/questions/10125881/send-a-message-from-javascript-running-in-a-browser-to-a-windows-batch-file
# e.g. curl --data 'command=left' -X POST http://localhost:8080/

GESTURE_NOBODY_HOME = [["2", "160"]]
GESTURE_SOMEBODY_HOME = [["2", "140"],["1","90"]]
GESTURE_CENTRE = [["1", "90"]]
GESTURE_HELLO = [["2","40"],["2","140"]]
GESTURE_LEAVING = [["2", "40"],["1","90"]]
GESTURE_LOOKING_ROUND = [["1", "60"],["1", "120"],["1", "90"]]
GESTURE_REVOLVE_ALL_LEFT = [["1", "180"]]
GESTURE_REVOLVE_ALL_RIGHT = [["1", "0"]]
GESTURE_A_BIT_RIGHT = [["1", "40", "p"]]
GESTURE_A_BIT_LEFT = [["1", "40", "n"]]
GESTURE_A_BIT_UP = [["2", "40", "p"]]
GESTURE_A_BIT_DOWN = [["2", "40", "n"]]

ser = serial.Serial('/dev/serial0', 9600)

@route('/', method=['OPTIONS', 'POST'])
def index():

    response.headers['Access-Control-Allow-Origin'] = '*'
    response.headers['Access-Control-Allow-Methods'] = 'PUT, GET, POST, DELETE, OPTIONS'
    response.headers['Access-Control-Allow-Headers'] = 'Origin, Accept, Content-Type, X-Requested-With, X-CSRF-Token'

    command = "none"

    if request.method == 'POST':
      command = request.POST['command']
      print command
      arduino_command = None
      if(command):

# used by the software mostly
        if(command == "gone"):
          arduino_command = GESTURE_NOBODY_HOME
        if(command == "arrived"):
          arduino_command = GESTURE_SOMEBODY_HOME

# used by the end user / frontend

        if(command == "hello"):
          arduino_command = GESTURE_HELLO
        if(command == "leaving"):
          arduino_command = GESTURE_LEAVING

        if(command == "left"):
          arduino_command = GESTURE_REVOLVE_ALL_LEFT
        if(command == "right"):
          arduino_command = GESTURE_REVOLVE_ALL_RIGHT


        if(command == "left_a_bit"):
          arduino_command = GESTURE_A_BIT_LEFT
        if(command == "right_a_bit"):
          arduino_command = GESTURE_A_BIT_RIGHT

        if(command == "down_a_bit"):
          arduino_command = GESTURE_A_BIT_DOWN
        if(command == "up_a_bit"):
          arduino_command = GESTURE_A_BIT_UP


# pass through for testing, e.g. 1 90 or 2 30

        if(command.startswith("1") or command.startswith("2")):
          arduino_command = [command.split(" ")]
          print(arduino_command)

# special for when the webrtc fails or for a manual stop

        if(command == "halt"):
          arduino_command = GESTURE_LEAVING

        if(command == "reboot"):
          arduino_command = GESTURE_LEAVING

# each subarray is a command
# motor 1 is the base (rotate)
# motor 2 is the head (up / down)

        for ac in arduino_command: 
          print(" ".join(ac)+"\n")
          ser.write(" ".join(ac)+"\n")
        
        if(command == "halt"):
          time.sleep(5)
          result = os.system("sudo halt")
        if(command == "reboot"):
          time.sleep(5)
          result = os.system("sudo reboot")

    response.set_header('Access-Control-Allow-Origin', '*')
    result = "ok: "+command
    return result

run(host='localhost', port=8080, reloader=True)

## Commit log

2017-07-18 Arduino code
2017-07-20 Add base templates
    [base1.dxf, base2.dxf]
2017-07-20 Servo horn! thanks barnoid
2017-07-20 Improve arduino instructions
2017-07-22 Fix some arduino typos
    [libbybot11.ino]
2017-07-27 Fix bugs in Arduino code
    [libbybot11.ino]
2018-07-30 Update readme to address bcm2835-v4l2 issues with V2 cameras
2018-08-19 Get the pin numbers right
2018-08-20 Improved servo commands
